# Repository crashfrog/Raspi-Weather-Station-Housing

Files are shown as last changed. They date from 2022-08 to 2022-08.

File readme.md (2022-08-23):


# Weather Stn
An anaerometer and atmospheric sampling station based on RasPi Zero W.

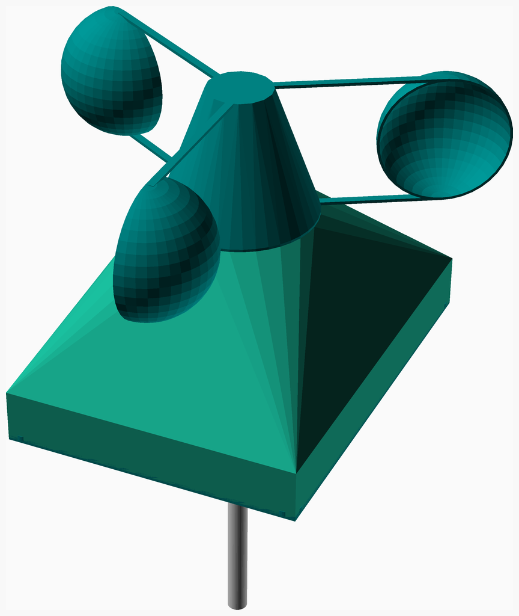
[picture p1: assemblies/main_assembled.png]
Main Assembly


<span></span>

---
## Table of Contents
1. [Parts list](#Parts_list)
1. [Housing Assembly](#housing_assembly)
1. [Pi Assembly](#pi_assembly)
1. [Plate Assembly](#plate_assembly)
1. [Spinner Assembly](#spinner_assembly)
1. [Main Assembly](#main_assembly)

<span></span>
[Top](#TOP)

---

## Parts list
| <span style="writing-mode: vertical-rl; text-orientation: mixed;">Housing</span> | <span style="writing-mode: vertical-rl; text-orientation: mixed;">Pi</span> | <span style="writing-mode: vertical-rl; text-orientation: mixed;">Plate</span> | <span style="writing-mode: vertical-rl; text-orientation: mixed;">Spinner</span> | <span style="writing-mode: vertical-rl; text-orientation: mixed;">Main</span> | <span style="writing-mode: vertical-rl; text-orientation: mixed;">TOTALS</span> |  |
|---:|---:|---:|---:|---:|---:|:---|
|  |  |  |  |  | | **Vitamins** |
| &nbsp;&nbsp;.&nbsp; | &nbsp;&nbsp;.&nbsp; | &nbsp;&nbsp;1&nbsp; | &nbsp;&nbsp;.&nbsp; | &nbsp;&nbsp;.&nbsp; |  &nbsp;&nbsp;1&nbsp; | &nbsp;&nbsp; BME680 Atmospheric Sensor STEMMA-QT |
| &nbsp;&nbsp;.&nbsp; | &nbsp;&nbsp;.&nbsp; | &nbsp;&nbsp;.&nbsp; | &nbsp;&nbsp;1&nbsp; | &nbsp;&nbsp;.&nbsp; |  &nbsp;&nbsp;1&nbsp; | &nbsp;&nbsp; Ball bearing 608-2RS 8mm x 22mm x 7mm |
| &nbsp;&nbsp;1&nbsp; | &nbsp;&nbsp;.&nbsp; | &nbsp;&nbsp;.&nbsp; | &nbsp;&nbsp;.&nbsp; | &nbsp;&nbsp;.&nbsp; |  &nbsp;&nbsp;1&nbsp; | &nbsp;&nbsp; Hall Effect Sensor |
| &nbsp;&nbsp;5&nbsp; | &nbsp;&nbsp;.&nbsp; | &nbsp;&nbsp;13&nbsp; | &nbsp;&nbsp;.&nbsp; | &nbsp;&nbsp;.&nbsp; |  &nbsp;&nbsp;18&nbsp; | &nbsp;&nbsp; Heatfit insert M2.5 |
| &nbsp;&nbsp;.&nbsp; | &nbsp;&nbsp;.&nbsp; | &nbsp;&nbsp;.&nbsp; | &nbsp;&nbsp;1&nbsp; | &nbsp;&nbsp;.&nbsp; |  &nbsp;&nbsp;1&nbsp; | &nbsp;&nbsp; Magnet, 5mm diameter, 1mm high |
| &nbsp;&nbsp;.&nbsp; | &nbsp;&nbsp;1&nbsp; | &nbsp;&nbsp;.&nbsp; | &nbsp;&nbsp;.&nbsp; | &nbsp;&nbsp;.&nbsp; |  &nbsp;&nbsp;1&nbsp; | &nbsp;&nbsp; Micro SD card |
| &nbsp;&nbsp;.&nbsp; | &nbsp;&nbsp;.&nbsp; | &nbsp;&nbsp;1&nbsp; | &nbsp;&nbsp;.&nbsp; | &nbsp;&nbsp;.&nbsp; |  &nbsp;&nbsp;1&nbsp; | &nbsp;&nbsp; Micro USB Panel Jack |
| &nbsp;&nbsp;.&nbsp; | &nbsp;&nbsp;.&nbsp; | &nbsp;&nbsp;1&nbsp; | &nbsp;&nbsp;.&nbsp; | &nbsp;&nbsp;.&nbsp; |  &nbsp;&nbsp;1&nbsp; | &nbsp;&nbsp; PMSA003I Air Particulate Sensor STEMMA-QT |
| &nbsp;&nbsp;.&nbsp; | &nbsp;&nbsp;2&nbsp; | &nbsp;&nbsp;.&nbsp; | &nbsp;&nbsp;.&nbsp; | &nbsp;&nbsp;.&nbsp; |  &nbsp;&nbsp;2&nbsp; | &nbsp;&nbsp; Pin header 2 x 1 |
| &nbsp;&nbsp;.&nbsp; | &nbsp;&nbsp;1&nbsp; | &nbsp;&nbsp;.&nbsp; | &nbsp;&nbsp;.&nbsp; | &nbsp;&nbsp;.&nbsp; |  &nbsp;&nbsp;1&nbsp; | &nbsp;&nbsp; Pin header 20 x 2 |
| &nbsp;&nbsp;.&nbsp; | &nbsp;&nbsp;1&nbsp; | &nbsp;&nbsp;.&nbsp; | &nbsp;&nbsp;.&nbsp; | &nbsp;&nbsp;.&nbsp; |  &nbsp;&nbsp;1&nbsp; | &nbsp;&nbsp; Raspberry Pi Zero |
| &nbsp;&nbsp;.&nbsp; | &nbsp;&nbsp;.&nbsp; | &nbsp;&nbsp;11&nbsp; | &nbsp;&nbsp;.&nbsp; | &nbsp;&nbsp;.&nbsp; |  &nbsp;&nbsp;11&nbsp; | &nbsp;&nbsp; Screw M2.5 cap x  5mm |
| &nbsp;&nbsp;.&nbsp; | &nbsp;&nbsp;.&nbsp; | &nbsp;&nbsp;.&nbsp; | &nbsp;&nbsp;.&nbsp; | &nbsp;&nbsp;4&nbsp; |  &nbsp;&nbsp;4&nbsp; | &nbsp;&nbsp; Screw M2.5 cap x  7mm |
| &nbsp;&nbsp;.&nbsp; | &nbsp;&nbsp;.&nbsp; | &nbsp;&nbsp;2&nbsp; | &nbsp;&nbsp;.&nbsp; | &nbsp;&nbsp;1&nbsp; |  &nbsp;&nbsp;3&nbsp; | &nbsp;&nbsp; Screw M2.5 cap x 15mm |
| &nbsp;&nbsp;.&nbsp; | &nbsp;&nbsp;.&nbsp; | &nbsp;&nbsp;.&nbsp; | &nbsp;&nbsp;.&nbsp; | &nbsp;&nbsp;1&nbsp; |  &nbsp;&nbsp;1&nbsp; | &nbsp;&nbsp; Smooth rod 8mm x 200mm |
| &nbsp;&nbsp;.&nbsp; | &nbsp;&nbsp;1&nbsp; | &nbsp;&nbsp;.&nbsp; | &nbsp;&nbsp;.&nbsp; | &nbsp;&nbsp;.&nbsp; |  &nbsp;&nbsp;1&nbsp; | &nbsp;&nbsp; SparkFun Qwiic HAT |
| &nbsp;&nbsp;6&nbsp; | &nbsp;&nbsp;6&nbsp; | &nbsp;&nbsp;29&nbsp; | &nbsp;&nbsp;2&nbsp; | &nbsp;&nbsp;6&nbsp; | &nbsp;&nbsp;49&nbsp; | &nbsp;&nbsp;Total vitamins count |
|  |  |  |  |  | | **3D printed parts** |
| &nbsp;&nbsp;1&nbsp; | &nbsp;&nbsp;.&nbsp; | &nbsp;&nbsp;.&nbsp; | &nbsp;&nbsp;.&nbsp; | &nbsp;&nbsp;.&nbsp; |  &nbsp;&nbsp;1&nbsp; | &nbsp;&nbsp;housing.stl |
| &nbsp;&nbsp;.&nbsp; | &nbsp;&nbsp;.&nbsp; | &nbsp;&nbsp;1&nbsp; | &nbsp;&nbsp;.&nbsp; | &nbsp;&nbsp;.&nbsp; |  &nbsp;&nbsp;1&nbsp; | &nbsp;&nbsp;plate.stl |
| &nbsp;&nbsp;.&nbsp; | &nbsp;&nbsp;.&nbsp; | &nbsp;&nbsp;.&nbsp; | &nbsp;&nbsp;1&nbsp; | &nbsp;&nbsp;.&nbsp; |  &nbsp;&nbsp;1&nbsp; | &nbsp;&nbsp;spinner.stl |
| &nbsp;&nbsp;1&nbsp; | &nbsp;&nbsp;.&nbsp; | &nbsp;&nbsp;1&nbsp; | &nbsp;&nbsp;1&nbsp; | &nbsp;&nbsp;.&nbsp; | &nbsp;&nbsp;3&nbsp; | &nbsp;&nbsp;Total 3D printed parts count |

<span></span>
[Top](#TOP)

---

## Housing Assembly
### Vitamins
|Qty|Description|
|---:|:---|
|1| Hall Effect Sensor|
|5| Heatfit insert M2.5|

### 3D Printed parts

| 1 x housing.stl |
|---|
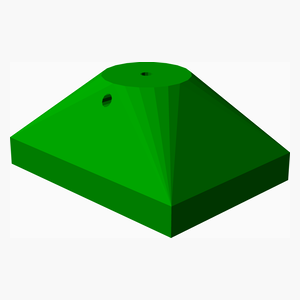
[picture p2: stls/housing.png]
housing.stl
|  

### Assembly instructions
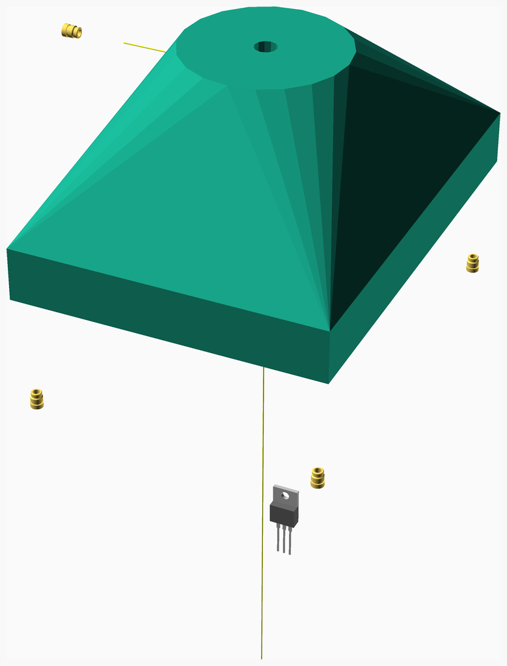
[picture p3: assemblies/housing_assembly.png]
housing_assembly


Heat-set inserts into the four plate mounting lugs and into the rod retaining lug.

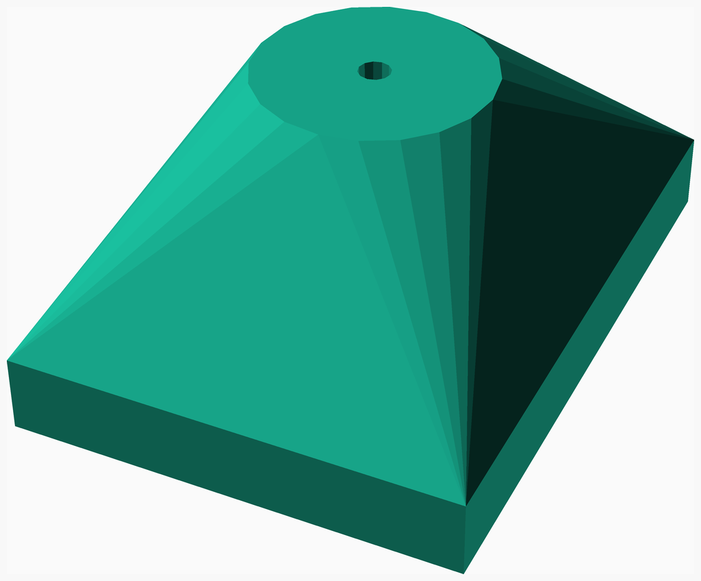
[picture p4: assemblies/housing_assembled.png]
housing_assembled


<span></span>
[Top](#TOP)

---

## Pi Assembly
### Vitamins
|Qty|Description|
|---:|:---|
|1| Micro SD card|
|2| Pin header 2 x 1|
|1| Pin header 20 x 2|
|1| Raspberry Pi Zero|
|1| SparkFun Qwiic HAT|

### Assembly instructions
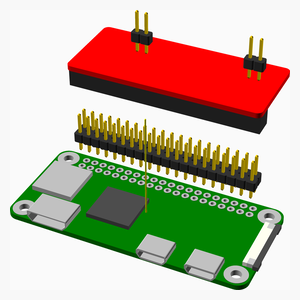
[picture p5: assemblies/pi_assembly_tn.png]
pi_assembly


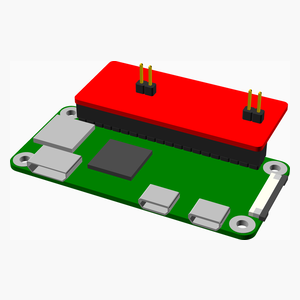
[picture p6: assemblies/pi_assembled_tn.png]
pi_assembled


<span></span>
[Top](#TOP)

---

## Plate Assembly
### Vitamins
|Qty|Description|
|---:|:---|
|1| BME680 Atmospheric Sensor STEMMA-QT|
|13| Heatfit insert M2.5|
|1| Micro USB Panel Jack|
|1| PMSA003I Air Particulate Sensor STEMMA-QT|
|11| Screw M2.5 cap x  5mm|
|2| Screw M2.5 cap x 15mm|

### 3D Printed parts

| 1 x plate.stl |
|---|
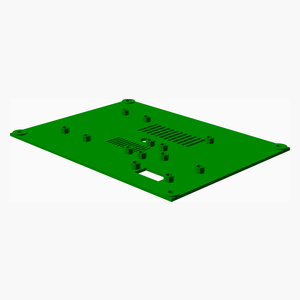
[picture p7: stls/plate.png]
plate.stl
|  

### Sub-assemblies

| 1 x pi_assembly |
|---|
| pi_assembled 

### Assembly instructions
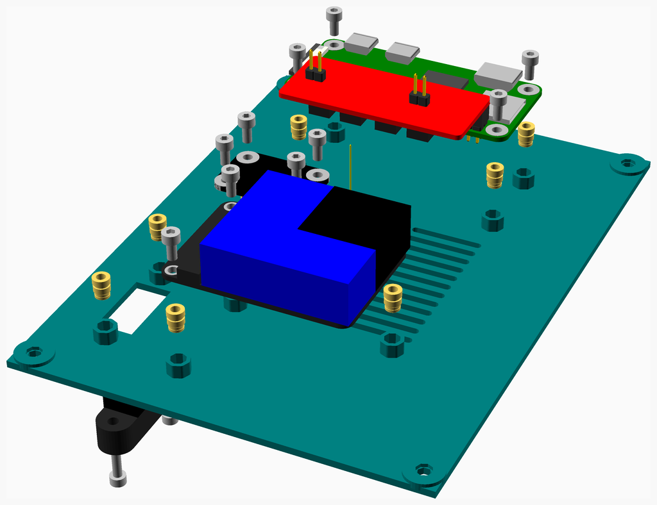
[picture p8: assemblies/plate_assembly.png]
plate_assembly


Insert the heat-set inserts.  
Mount the components.  
Mount the panel-mount USB connector, and connect to the RPi0.  
Connect the components using STEMMA-QT cables.  

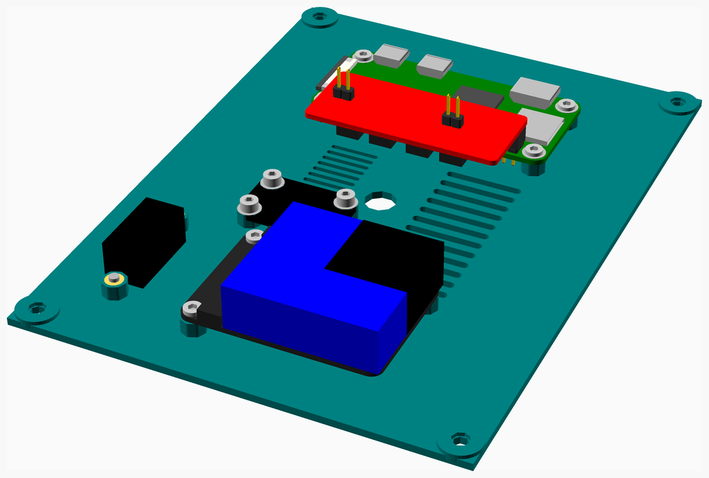
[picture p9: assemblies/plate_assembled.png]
plate_assembled


<span></span>
[Top](#TOP)

---

## Spinner Assembly
### Vitamins
|Qty|Description|
|---:|:---|
|1| Ball bearing 608-2RS 8mm x 22mm x 7mm|
|1| Magnet, 5mm diameter, 1mm high|

### 3D Printed parts

| 1 x spinner.stl |
|---|
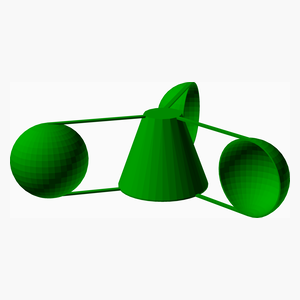
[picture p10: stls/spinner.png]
spinner.stl
|  

### Assembly instructions
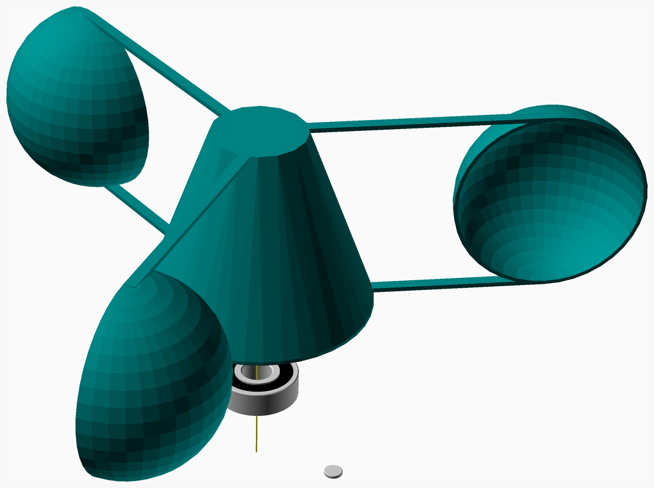
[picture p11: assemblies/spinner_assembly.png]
spinner_assembly


Press-fit the skate bearing into the anemometer spinner.  
Epoxy or glue the magnet into the magnet void.  

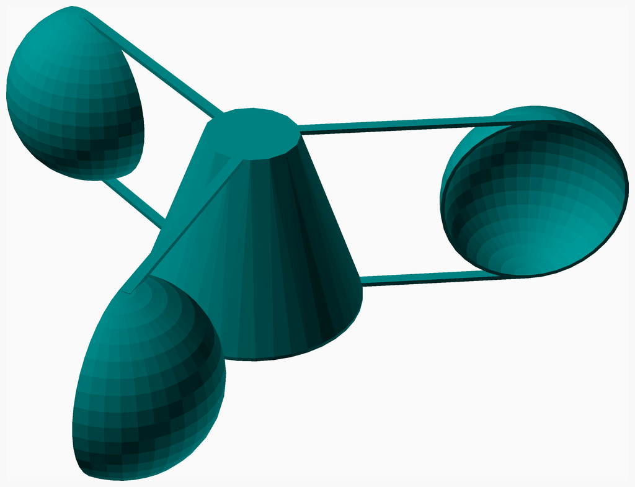
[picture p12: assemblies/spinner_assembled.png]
spinner_assembled


<span></span>
[Top](#TOP)

---

## Main Assembly
### Vitamins
|Qty|Description|
|---:|:---|
|4| Screw M2.5 cap x  7mm|
|1| Screw M2.5 cap x 15mm|
|1| Smooth rod 8mm x 200mm|

### Sub-assemblies

| 1 x housing_assembly | 1 x plate_assembly | 1 x spinner_assembly |
|---|---|---|
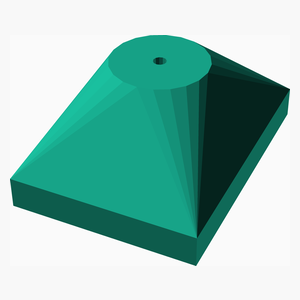
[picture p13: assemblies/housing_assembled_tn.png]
housing_assembled
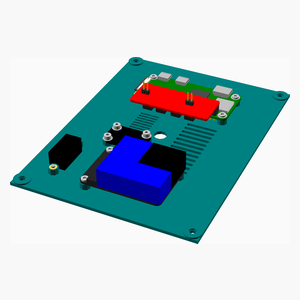
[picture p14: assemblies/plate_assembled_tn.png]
plate_assembled
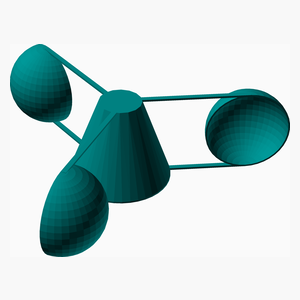
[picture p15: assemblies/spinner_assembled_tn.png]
spinner_assembled
|  |  |  

### Assembly instructions
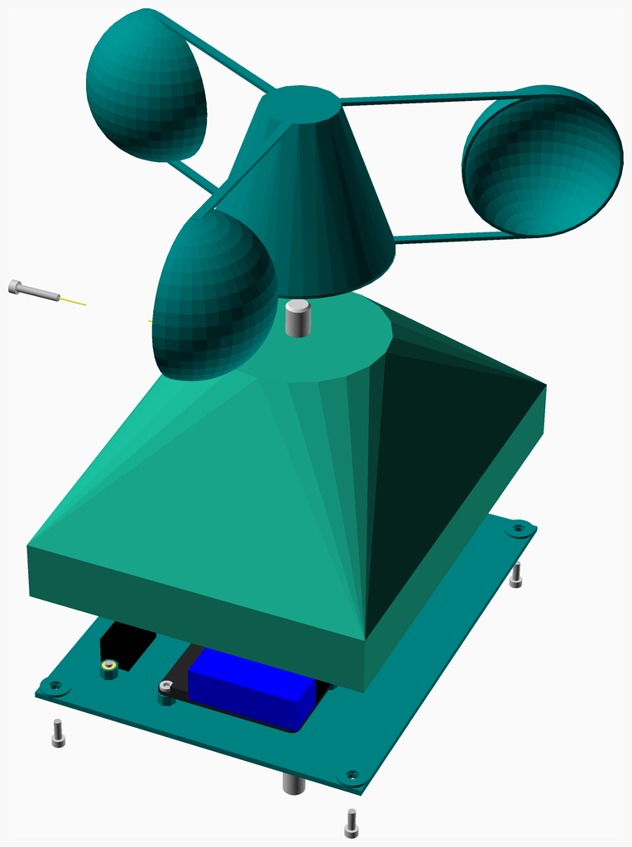
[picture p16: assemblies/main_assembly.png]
main_assembly


Assembly instructions  
Mount the anemometer spinner on top of the mounting rod.  
Slide the housing up the rod and mount with an M2.5x15 screw.  
Connect the hall effect sensor to the RasPI.  
Mate the PCB base to the housing using M2.5x5 screws.  

main_assembled

<span></span>
[Top](#TOP)

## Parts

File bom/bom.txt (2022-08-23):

Vitamins:
 H           S
 o           p
 u        P  i
 s  M     l  n
 i  a     a  n
 n  i  P  t  e
 g  n  i  e  r
  |  | 1|  |  |  1 Micro SD card
 1|  |  |  |  |  1 Hall Effect Sensor
  |  |  |  | 1|  1 Ball bearing 608-2RS 8mm x 22mm x 7mm
 5|  |  |13|  | 18 Heatfit insert M2.5
  |  |  |  | 1|  1 Magnet, 5mm diameter, 1mm high
  |  |  | 1|  |  1 BME680 Atmospheric Sensor STEMMA-QT
  |  |  | 1|  |  1 PMSA003I Air Particulate Sensor STEMMA-QT
  |  | 1|  |  |  1 SparkFun Qwiic HAT
  |  | 1|  |  |  1 Raspberry Pi Zero
  |  |  | 1|  |  1 Micro USB Panel Jack
  |  | 2|  |  |  2 Pin header 2 x 1
  |  | 1|  |  |  1 Pin header 20 x 2
  | 1|  |  |  |  1 Smooth rod 8mm x 200mm
  | 1|  | 2|  |  3 Screw M2.5 cap x 15mm
  |  |  |11|  | 11 Screw M2.5 cap x  5mm
  | 4|  |  |  |  4 Screw M2.5 cap x  7mm

Printed:
 1|  |  |  |  |  1 housing.stl
  |  |  | 1|  |  1 plate.stl
  |  |  |  | 1|  1 spinner.stl

Assemblies:
  1 housing_assembly
  1 main_assembly
  1 pi_assembly
  1 plate_assembly
  1 spinner_assembly

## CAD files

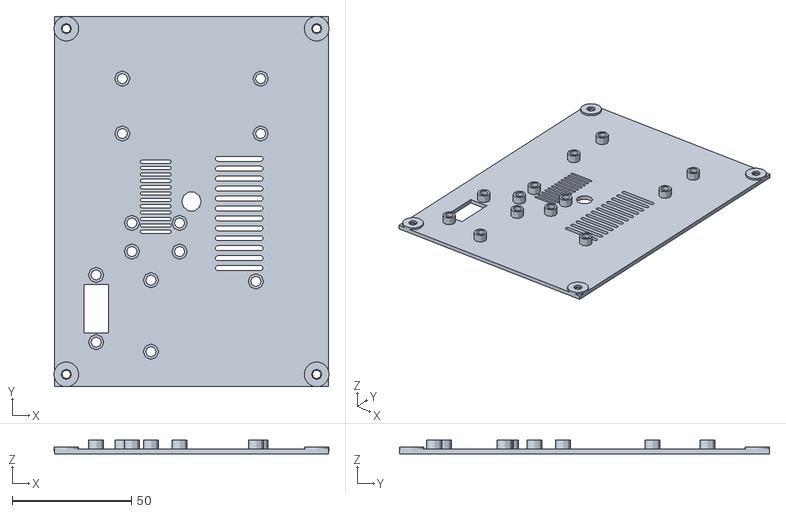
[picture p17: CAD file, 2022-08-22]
stls/plate.stl
115.3 x 155.3 x 5.80

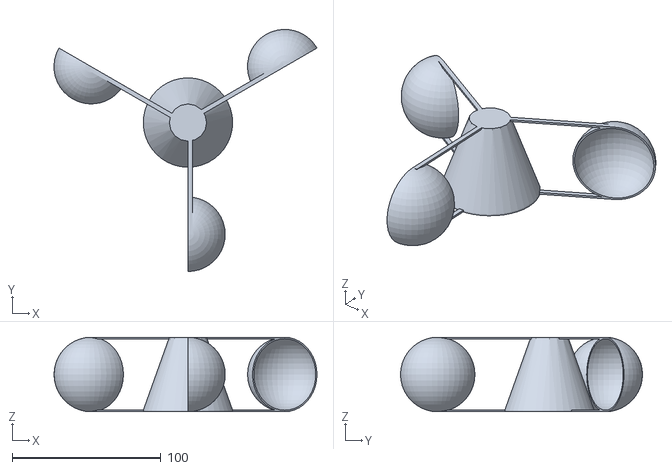
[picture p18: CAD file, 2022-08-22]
stls/spinner.stl
176.5 x 162.5 x 50.0

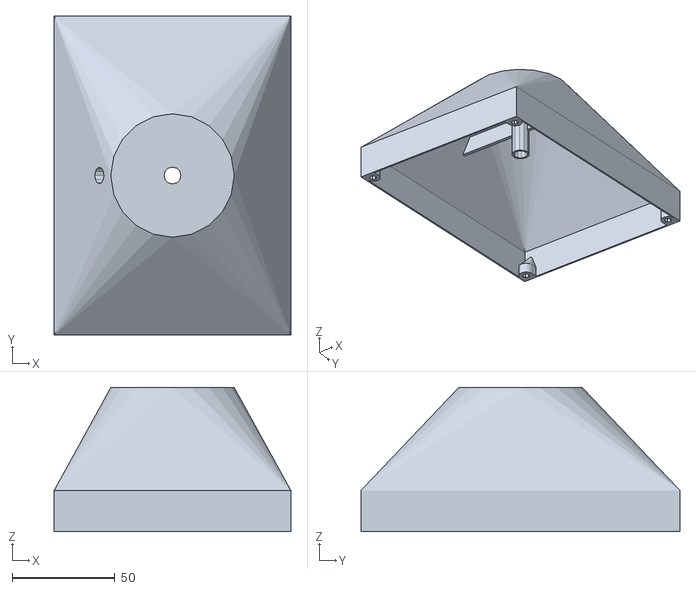
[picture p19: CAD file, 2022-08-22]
stls/housing.stl
115.0 x 155.0 x 70.0

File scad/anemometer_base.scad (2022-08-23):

//! An anaerometer and atmospheric sampling station based on RasPi Zero W.

include <NopSCADlib/lib.scad>

use <Round-Anything/polyround.scad>

$explode=1;
$fn=40;

tallness = 70;
base_width = 155;
base_height = 115;
magnet = ["MAG5x1", "Magnet", 5, 0, 1, .25];
bearing = BB608;

module position(w, h){
    for (p=[-1,1], q=[-1,1]){
        translate([q*h/2, p*w/2, 0]) children();
    }
}

module position_for_raspi(){
    translate([0,40,0]) rotate([0,0,180]) children();
}

module position_for_bme680(w=20, h=11){
    translate([-15,-15,0]) rotate([0,0,90]) children();
}

module position_for_PMSA003I(w=30, h=45){
    translate([5,-48,0]) children();
}

module position_jack(){
    translate([-40,-45,0]) rotate([0,0,90]) children();
}

module position_lugs(z=0){
    for (coord=housing_plate_lugs){
        translate([coord[0], coord[1], z-.02]) rotate([0,0,coord[2]]) children();
    }
}

module position_retaining_screw(z=tallness-10){
    translate([-3,0,z]) rotate([0,-90,0]) children();
}

s=4.8; //standoff height




BME680 = ["BME680", "BME680 Atmospheric Sensor STEMMA-QT",
    18, 26, 1.4, 3, 2.65, 6, "black", false, [//holes
                                             [3, 3],
                                             [18-3,3],
                                             [3,26-3],
                                             [18-3,26-3],], 
                                             [//components
                                               [9,13,0,"chip",4,4,1,"silver"],
                                               [9,2,0,"chip",6,4,3,grey(15)],
                                               [9,24,0,"chip",6,4,3,grey(15)],
                                             ], 
                                             []
];

PMSA003I = ["PMSA003I", "PMSA003I Air Particulate Sensor STEMMA-QT",
    50,35,1.4,3,2.65,4,grey(15), false, [[3,2.5],
                                        //[50-3,3],
                                        [3,35-2.5],
                                        [50-3,35-3]],
                                        [//components
                                            [31,17.5,0,"chip",38,35,11.9,"blue"],
                                            [40,25,0,"chip",20.1,20.1,12.1,"black"],
                                            [8.5,2,0,"chip",6,4,3,grey(15)],
                                            [8.5,33,0,"chip",6,4,3,grey(15)],
                                        ],
                                        [],
];

QWIIC_HAT = ["QWIIC_HAT", "SparkFun Qwiic HAT",
    22, 52, 1.4, 1.5, 2.65, 4, "red", false, [],
    [//components
        [18.5,26,90,"2p54socket", 20, 2, false, 5, true],
        [2.5,40,90,"chip",6,4,3,grey(15)],
        [2.5,31,90,"chip",6,4,3,grey(15)],
        [2.5,21,90,"chip",6,4,3,grey(15)],
        [2.5,12,90,"chip",6,4,3,grey(15)],
    ],
    [],
];



USB_PANEL = ["musb_jack", "Micro USB Panel Jack", 
     36, 10, 8,4.9,3,2,grey(15), false, 
     [//holes
        [4,5],
        [27+5.2,5],
     ],
     [//components
        [18,6,[0,-90,90],"usb_uA",true,"red"],
        [18,5,0,"chip",20.2,10.2,12,"black"],
     ],[]
];



//! Assembly instructions  
//! Mount the anemometer spinner on top of the mounting rod.  
//! Slide the housing up the rod and mount with an M2.5x15 screw.  
//! Connect the hall effect sensor to the RasPI.  
//! Mate the PCB base to the housing using M2.5x5 screws.  
module main_assembly()
assembly("main"){
    explode(30, explode_children=true) translate([0,0,tallness])  spinner_assembly();
    explode(-40, explode_children=true) plate_assembly();
    translate([0,0,-20]) rod(8,200,center=true);
    explode(-60) position_lugs(0) rotate([0,180,0]) screw(M2p5_cap_screw, 7);
    position_retaining_screw() explode(50, explode_children=true) translate([0,0,23]) screw(M2p5_cap_screw, 15);
    housing_assembly();
}

module spinner_cup(r=30, t=1, r2=80, top=true){
    translate([0,0,r]) 
        difference(){
            intersection(){
                union(){
                    sphere(r=r);
                    t=1.2;
                    translate([1.5,r2/2,-r+(t/2)]) cube([3, r2, t], center=true);
                    if (top){
                        translate([1.5,r2/2,r-(t/2)]) cube([3, r2, t], center=true);
                    }
                }

            translate([r/2,0,0]) cube([r, r2*2, r*2], center=true);
        }
        
        sphere(r=r-t);
    }
}




module spinner_stl(c=3, cr=25, r=75)
color("teal") stl("spinner"){
    difference(){
        union(){
            for (p=[1:c]){
                rotate([0,0,p*(360/c)]) translate([0,0,0]) union(){
                    translate([0,-r,0]) spinner_cup(r=cr, r2=r);
                }
            }
            hull() {
                cylinder(h=1, d=60);
                translate([0,0,cr*2-1]) cylinder(h=1, d=cr, $fn=16);
            }
        }
        translate([0,0,-.01]) cylinder(h=bb_width(bearing)+0.2, d=bb_diameter(bearing)+0.2, $fn=12);
        translate([22.5,0,-.01]) cylinder(h=magnet_h(magnet)+0.2, d=magnet_od(magnet)+0.2, $fn=12);
    }
}




//! Press-fit the skate bearing into the anemometer spinner.  
//! Epoxy or glue the magnet into the magnet void.  
module spinner_assembly()
assembly("spinner"){
    explode(-20) translate([0,0,bb_width(bearing)/2]) ball_bearing(bearing);
    explode(-40) translate([22.5,0,0]) magnet(magnet);
    explode(10) rotate([0,0,0]) color("teal") spinner_stl();
}





module enc_hull(w=base_width, h=base_height, z=tallness-1){
    hull(){
        translate([0,0,z]) cylinder(h=1, d=60, $fn=20);
        translate([0,0,10]) cube([h,w,20], center=true);
        //position_for_raspi() pi_assembly();
        //position_for_PMSA003I() pcb(PMSA003I);
    }
}



module vents(n=5, h=20, w=40){
    vh=h;
    vw=w/n/2;
    r=vw/2;
    linear_extrude(20, center=true, convexity=n) translate([-h/2,(-w/2)+vw/2,0]) for (p=[1:n]){
        translate([0,(p-1)*(w/n),0]) polygon(polyRound([
                [0,0,r],
                [0,vw,r],
                [vh,vw,r],
                [vh,0,r],
            ], fn=3));
    }
}



w=5;

housing_plate_lugs = [[base_height/2-w, base_width/2-w, -90],
                      [-base_height/2+w, base_width/2-w, -90],
                      [base_height/2-w, -base_width/2+w, 90],
                      [-base_height/2+w, -base_width/2+w, 90],
                     ];




module housing_stl()
stl("housing"){
     color("teal", alpha=($explode==0) ? 0.05 : 1.0) difference(){
        enc_hull();
        position_retaining_screw() translate([0,0,12]) insert_hole(F1BM2p5, counterbore = 10, horizontal = true);
        position_retaining_screw() translate([0,0,22.8]) cylinder(h=base_height/2, d=8, $fn=12);
        translate([0,0,-20]) cylinder(h=200, d=8.2, $fn=12, center=true);
        difference(){
            translate([0,0,-1]) scale([.985,.989,1.005]) enc_hull();
            translate([0,0,30]) cylinder(h=70, d=8.2+2, $fn=12);
            translate([-base_width/2,0,45]) cube([base_width,2,base_height]);
            position_lugs(0) rotate([0,180,0]) insert_lug(F1BM2p5, wall=2, extension=4);
            position_retaining_screw() translate([0,0,0]) cylinder(h=base_height/2, d=10, $fn=12);
            // //mounting post for hall effect sensor
            translate([0,22.5,tallness]) cube([10,3,10], center=true);
        }
    }
}



//! Heat-set inserts into the four plate mounting lugs and into the rod retaining lug.
module housing_assembly()
assembly("housing"){
    explode(-45) position_lugs(0) rotate([0,180,0]) insert(F1BM2p5);
    position_retaining_screw() explode(50) translate([0,0,23]) insert(F1BM2p5);
    explode(-200) translate([0,22.5,tallness-3]) rotate([90,0,0]) TO220("Hall Effect Sensor");
    
    housing_stl(); //leave this last
}
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

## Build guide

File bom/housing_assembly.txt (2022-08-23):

housing_assembly:
Vitamins:
  1 Hall Effect Sensor
  5 Heatfit insert M2.5

Printed:
  1 housing.stl

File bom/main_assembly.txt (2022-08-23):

main_assembly:
Vitamins:
  1 Smooth rod 8mm x 200mm
  1 Screw M2.5 cap x 15mm
  4 Screw M2.5 cap x  7mm

Assemblies:
  1 housing_assembly
  1 plate_assembly
  1 spinner_assembly

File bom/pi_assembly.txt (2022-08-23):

pi_assembly:
Vitamins:
  1 Micro SD card
  1 SparkFun Qwiic HAT
  1 Raspberry Pi Zero
  2 Pin header 2 x 1
  1 Pin header 20 x 2

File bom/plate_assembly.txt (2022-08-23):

plate_assembly:
Vitamins:
 13 Heatfit insert M2.5
  1 BME680 Atmospheric Sensor STEMMA-QT
  1 PMSA003I Air Particulate Sensor STEMMA-QT
  1 Micro USB Panel Jack
  2 Screw M2.5 cap x 15mm
 11 Screw M2.5 cap x  5mm

Printed:
  1 plate.stl

Assemblies:
  1 pi_assembly

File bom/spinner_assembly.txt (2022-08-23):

spinner_assembly:
Vitamins:
  1 Ball bearing 608-2RS 8mm x 22mm x 7mm
  1 Magnet, 5mm diameter, 1mm high

Printed:
  1 spinner.stl

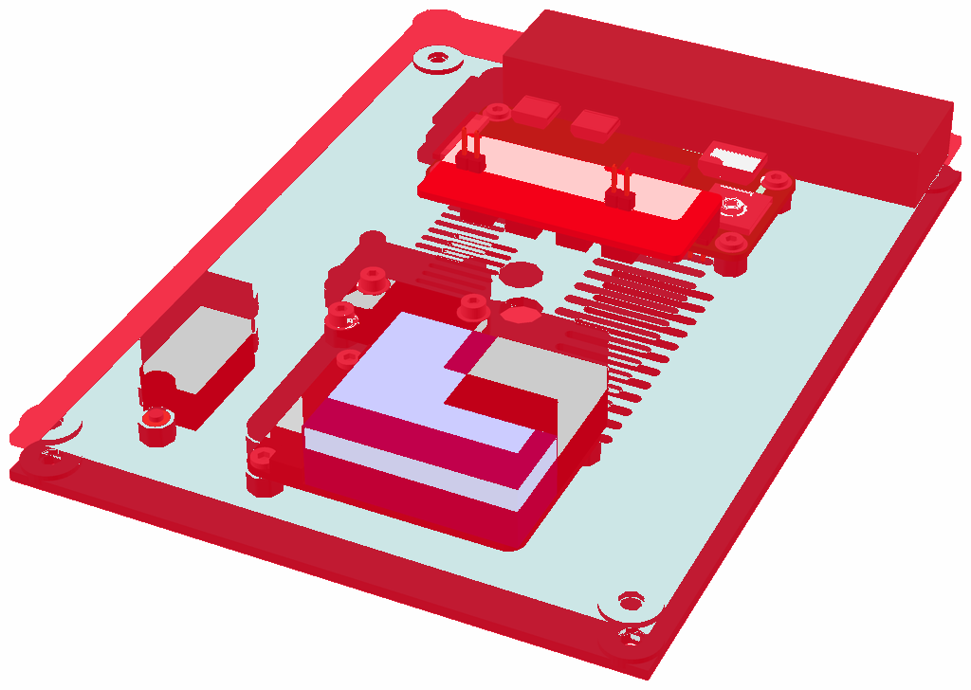
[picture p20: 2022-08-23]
assemblies/plate_assembled_diff.png

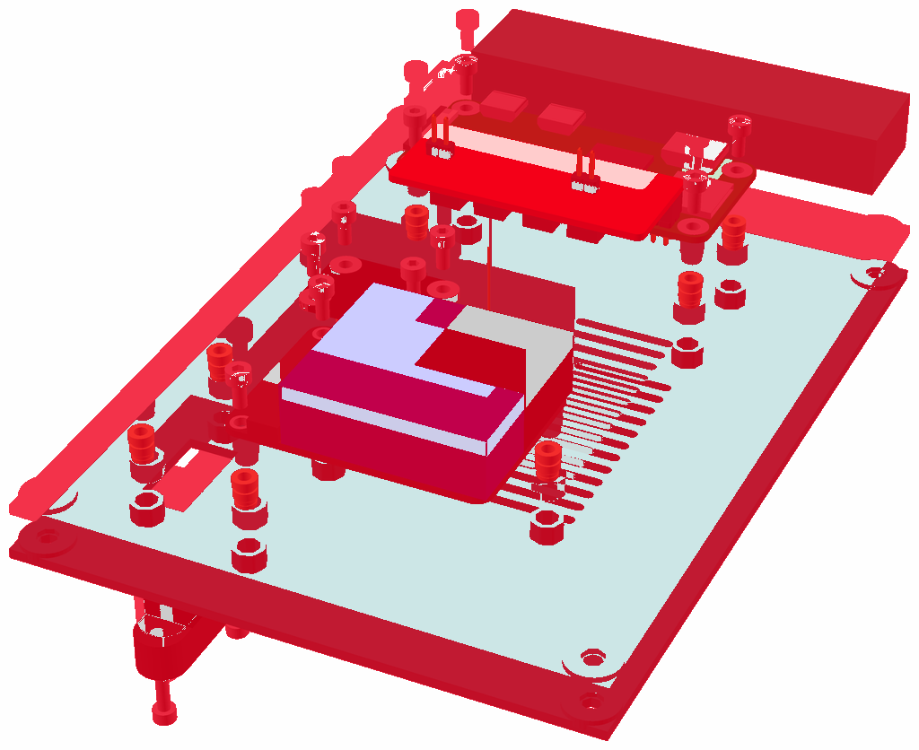
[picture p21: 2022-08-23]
assemblies/plate_assembly_diff.png

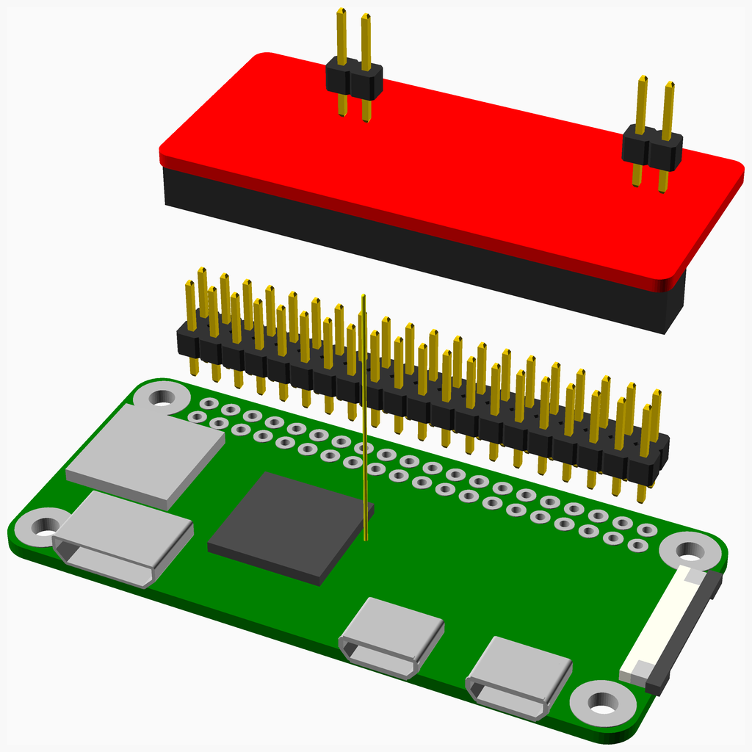
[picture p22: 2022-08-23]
assemblies/pi_assembly.png

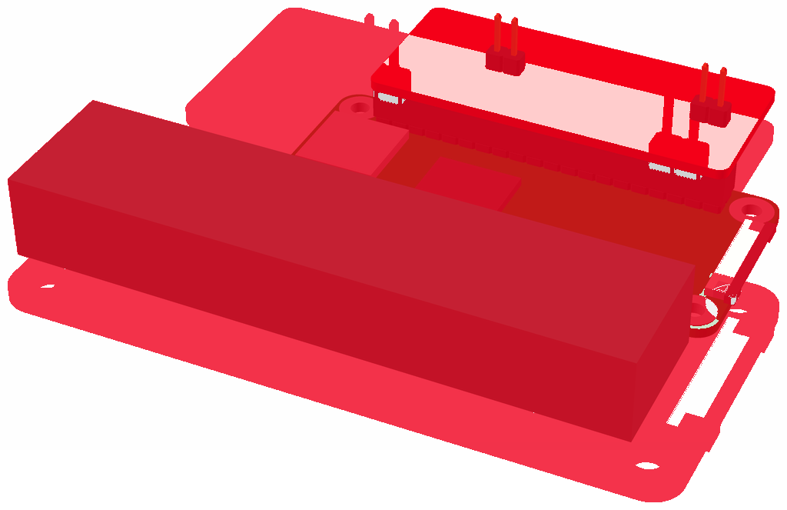
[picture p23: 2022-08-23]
assemblies/pi_assembled_diff.png

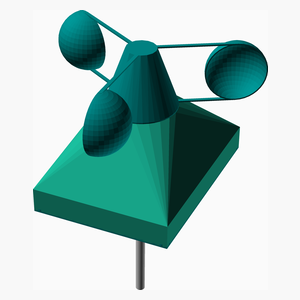
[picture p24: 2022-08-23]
assemblies/main_assembled_tn.png

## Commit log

2022-08-18 refined dimensions
    [anemometer_base.scad]
2022-08-22 working commit
    [anemometer_base.scad, housing.stl, plate.stl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]
2022-08-23 complete project
    [Anemometer_Oberteil.stl, bom.csv]
2022-08-23 update to project
    [anemometer_base.scad]
